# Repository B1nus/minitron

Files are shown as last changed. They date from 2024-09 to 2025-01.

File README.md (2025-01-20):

# Minitron
Turn your Prusa Mini into an upside-down CoreXY 3D Printer. This github repository covers the software side of the project, for build instructions and the bill of materials check out [the printables page](https://www.printables.com/model/1022602-minitron).

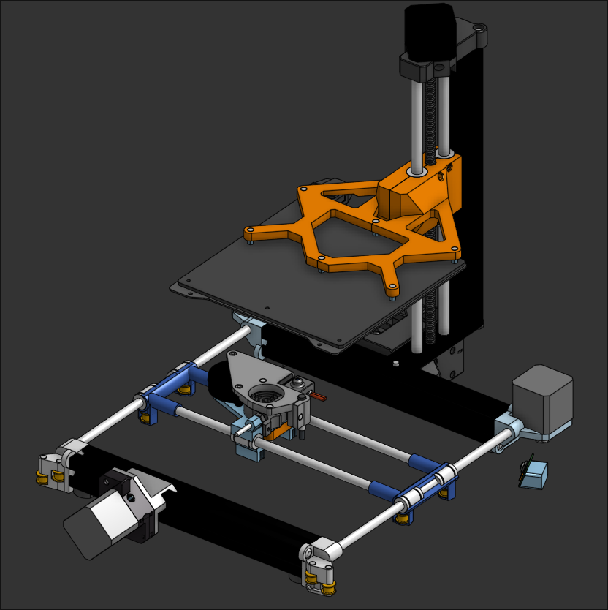
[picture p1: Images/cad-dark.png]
Screenshot of the positron CAD project


# Minitron in action
Gif of the minitron printing

# The first print
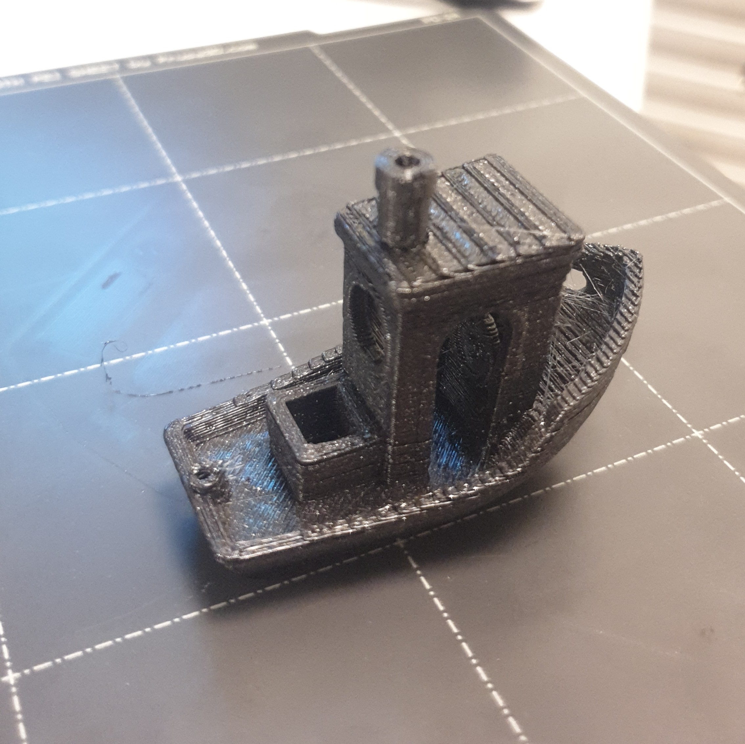
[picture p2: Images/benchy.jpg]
Picture of my first successfull print on the minitron


# WARNING!
The printer does work, but there are problems with this design:
- Loose belts (add an adjustable belt tension on the corner pieces)
- slanted and wobbly bed (add more plastic)
- extruder cable too short (use an extension cable)

# MainsailOS
MainsailOS is the operating system you will run on your control board (the raspberry pi). Mainsail handles the webinterface, scheduling prints, sending gcode and basically anything except communication with hardware which is the Buddy Boards job. [Install Mainsail here](https://docs-os.mainsail.xyz/getting-started/raspberry-pi-os-based). If you don't fell comfortable with Klipper and Mainsail you can try [this modified buddy board firmware](https://github.com/Snake-Edition/P32-FW/releases). Please note that you won't have a place to mount the LCD screen, as this printer is designed to use Mainsail's web interface instead of the LCD.

If you're using the rtl8188eu wifi adapter you should follow [these instruction](#rtl8188eu) to get wifi working.

## Installing Klipper
To install third party firmware you need to put your printer into DFU mode. Do this by following [the official instructions](https://help.prusa3d.com/article/flashing-custom-firmware-mini_14). Basically you need to cut the appendix and then short circuit two pins at the same time as switching on the printer. Connect the printer to your Raspberry Pi and proceed with these commands:

First run `$ cd ~/klipper`
Then `$ make menuconfig` and choose:
- Enable extra low-level configuration options
- STMicroelectronics STM32
- STM32F407
- No Bootloader
- Clock Reference 12 Mhz crystal
- Communication interface USB (on PA11/PA12)

Now run `lsusb` and look for a device with "DFU" in the name. If you can't find it, chances are the printer is not in DFU mode or the cable to the printer isn't working. To check if the printer is in DFU mode, turn it off and connect the LCD to the board. After putting it into DFU mode the screen should be blinding white.

When you've found the DFU device run `make flash FLASH_DEVICE=[insert id here]` with the id you found with `lsusb`.

# Configuration
My printer configuration is backed up automatically to this repository in *printer_data/config*. Feel free to use my config files. Don't forget to change the `rotation_distance` to `32` in the *printer.cfg* file if you're using the stock extruder. My prusa slicer profiles are also in this repository in the folder *prusa_profiles*.

Learn more about Klipper from their [documentation](https://www.klipper3d.org/pressure_advance.html).

# Extras
## Custom extruder and lid
I have some more [prusa mini mods on my printables account](https://www.printables.com/@Binus_2239073/models). It's up to you if you want these mods as well. The stock parts work just fine to.
### Camera
Check crowsnests logs to find the search path to your camera. Set *cam > device* in the file *crowsnest.conf* to this path. Sometimes it takes a while for the camera to load, you might need to refresh the page as well.

### Remote Control (Octoeverywhere)
Follow [their official instructions](https://octoeverywhere.com/dashboard?source=mainsail_docs). To learn of other solutions visit [mainsails page](https://docs.mainsail.xyz/overview/quicktips/remote-access).

### Backups
I broke my sd card once. Not fun. Nowdays I always backup my config files to github with [klipper-backup.git](https://github.com/Staubgeborener/klipper-backup?tab=readme-ov-file). Follow the instructions in their [documentation](https://klipperbackup.xyz/).

# Technical detail
### rtl8188eu
This specific driver caused me some trouble. To fix it, install the driver with this [excellent tutorial](https://gist.github.com/MBing/de297a8ae5e8a191c55a67a568d20d31) by [MBing](https://gist.github.com/MBing). If you want to choose a specific ip address change your /etc/interfaces file to something like this:
```
auto wlan0
iface wlan0 inet static
address [insert ip address]
netmask [insert netmask]
gateway [insert gateway]
broadcast [insert broadcast]
wpa-conf /etc/wpa_supplicant/wpa_supplicant.conf
```
Get the values by running ```ifconfig``` on another device connected to the same wifi.

# Credit
Credit to Prusa for the Prusa Mini, Kralyn for the Positron printer and Voxolite for the JourneyMaker. I wouldn't have been able to make this printer without you.

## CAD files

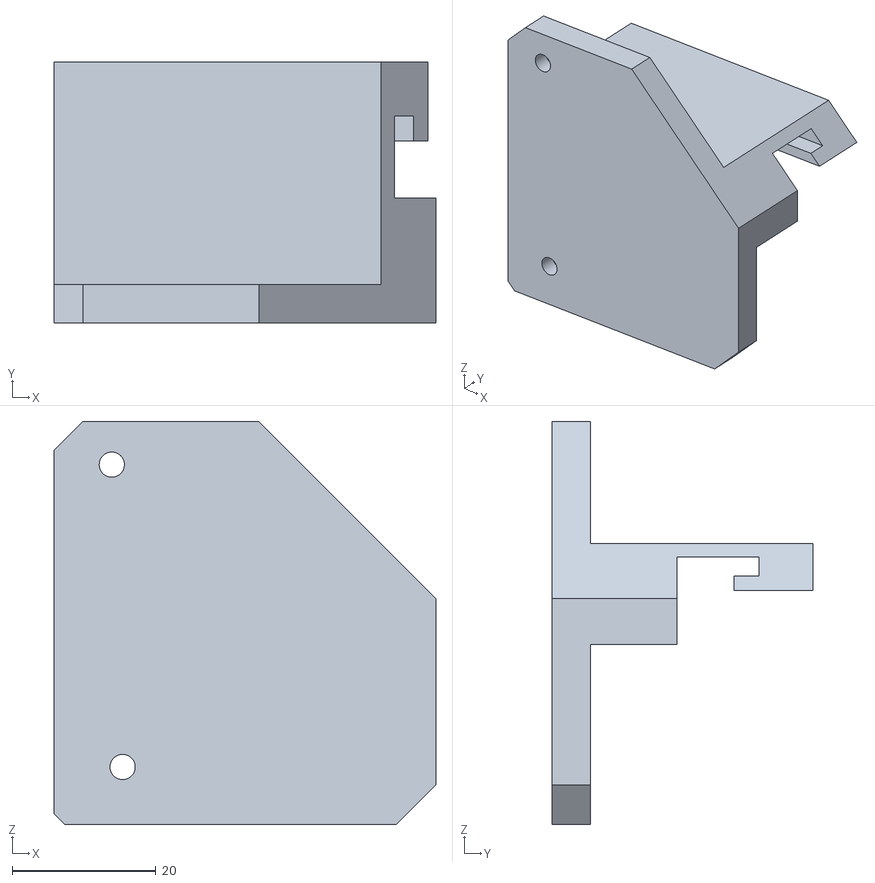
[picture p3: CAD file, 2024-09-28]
CAD/STL/Extruder Mount.stl
53.0 x 36.2 x 56.0

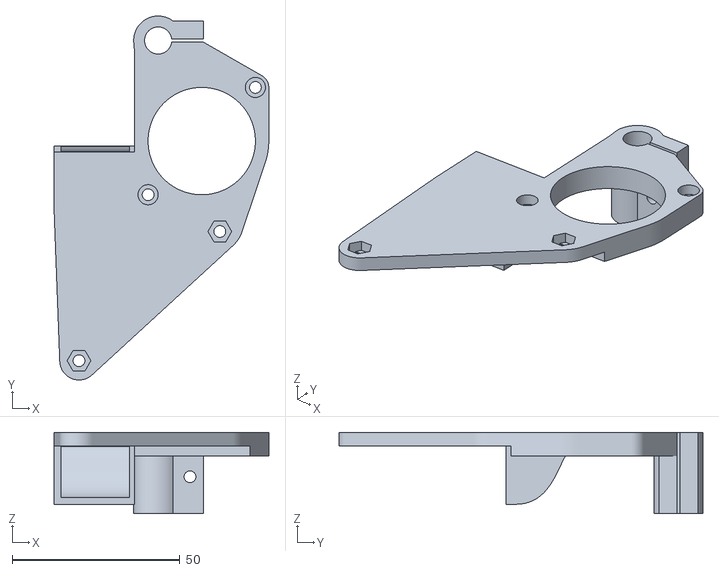
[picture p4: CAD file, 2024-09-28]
CAD/STL/Toolhead Top.stl
64.0 x 108.5 x 24.2

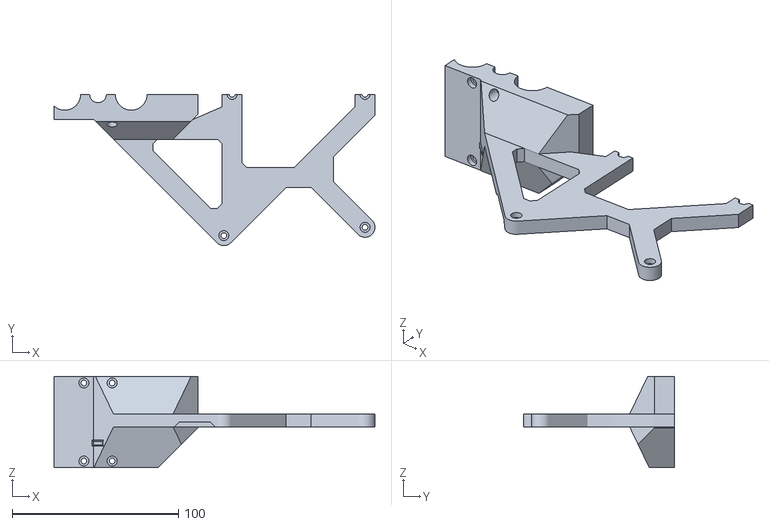
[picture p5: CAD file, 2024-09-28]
CAD/STL/Bed Carriage LEFT.stl
193.2 x 91.0 x 55.0

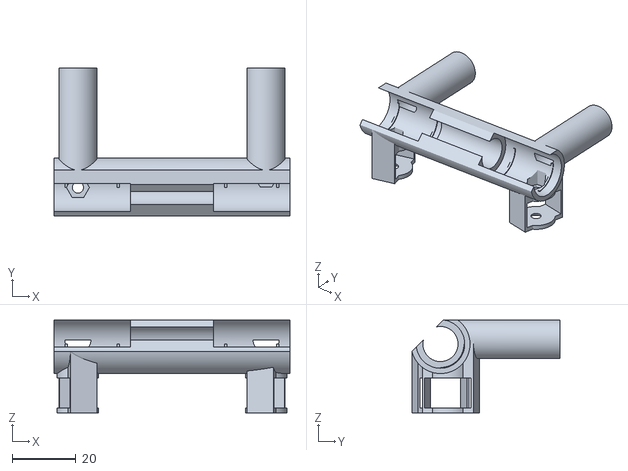
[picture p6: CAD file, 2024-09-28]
CAD/STL/Slider LEFT.stl
74.0 x 46.5 x 29.1

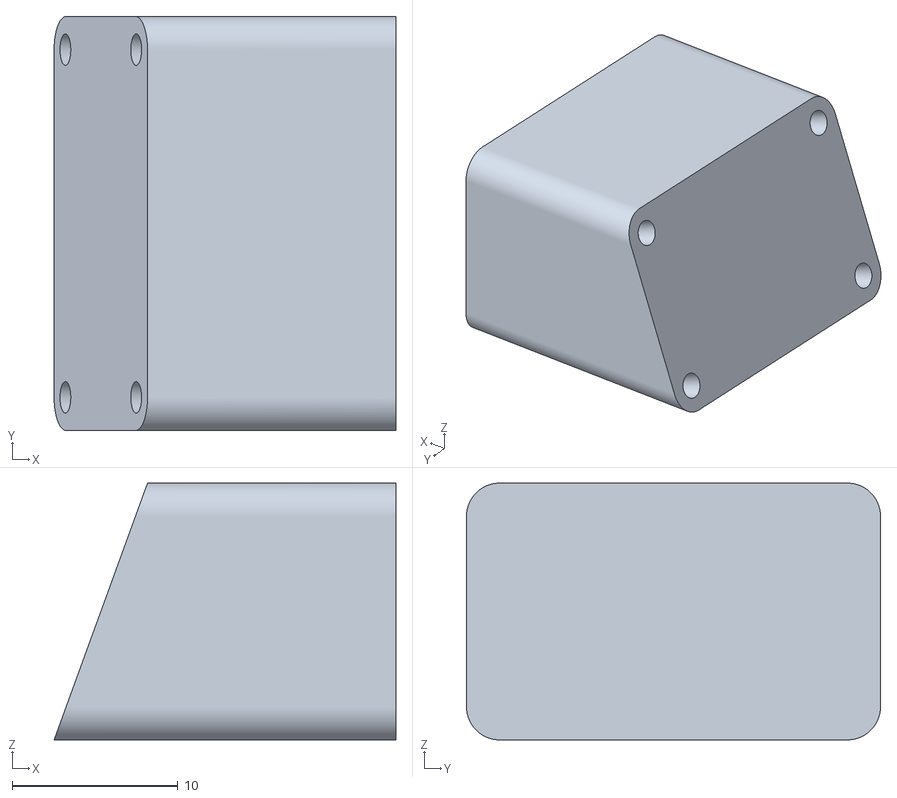
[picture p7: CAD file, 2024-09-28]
CAD/STL/Cam Mount.stl
20.6 x 25.0 x 15.5

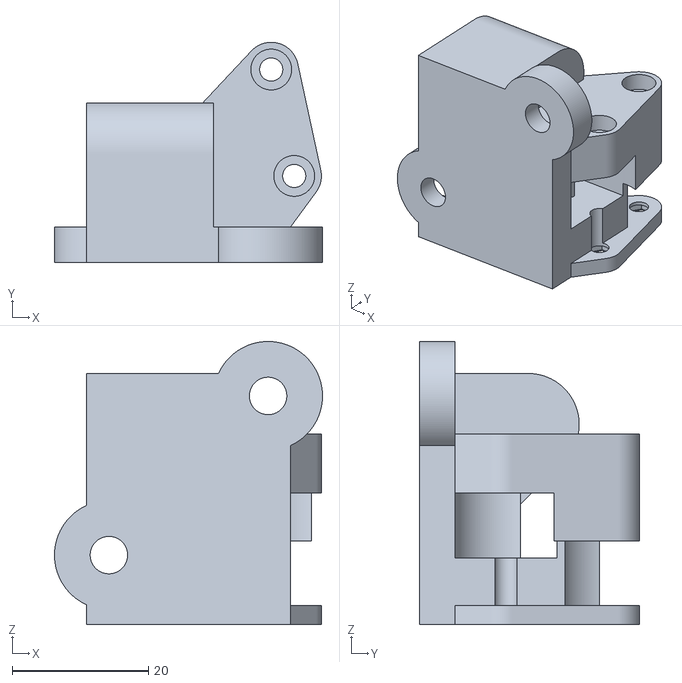
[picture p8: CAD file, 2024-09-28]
CAD/STL/Corner RIGHT.stl
39.4 x 32.4 x 41.6

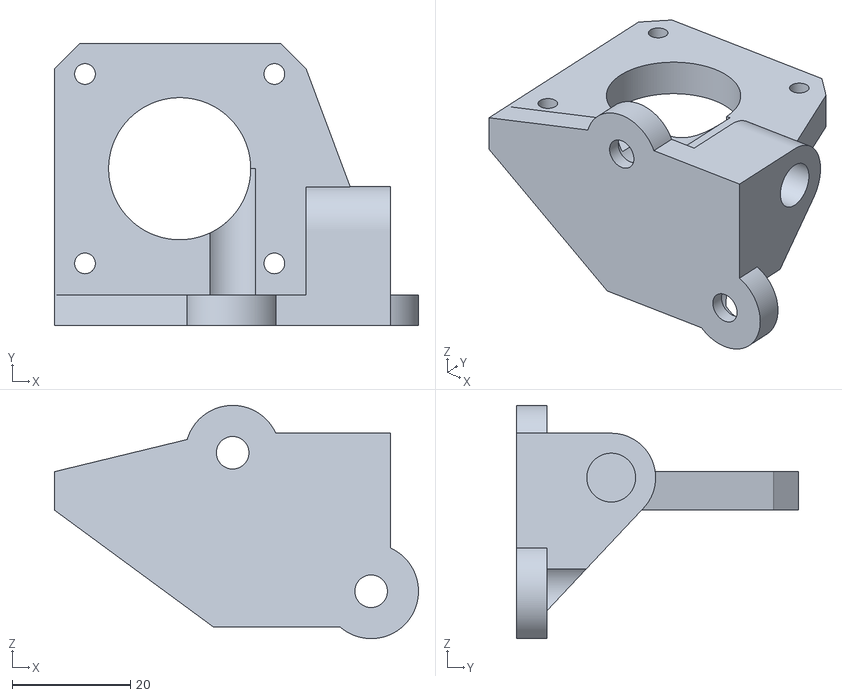
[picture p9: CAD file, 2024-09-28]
CAD/STL/Motor Corner RIGHT.stl
61.5 x 47.6 x 39.4

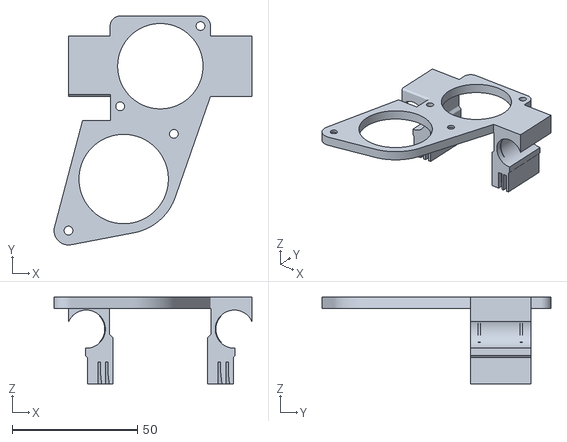
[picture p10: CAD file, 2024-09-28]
CAD/STL/Toolhead Bottom.stl
78.8 x 91.2 x 34.7

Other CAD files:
CAD/STL/Bed Carriage RIGHT.stl
CAD/STL/Slider RIGHT.stl
CAD/STL/Corner LEFT.stl
CAD/STL/Motor Corner LEFT.stl

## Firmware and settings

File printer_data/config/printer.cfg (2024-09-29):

#Exclude object support, needs [file_manager] > enable_object_processing to be enabled in moonraker.cfg
[exclude_object]
[include mainsail.cfg]
[include shell_command.cfg]
[include macros.cfg]

[stepper_x]
step_pin: PD1
dir_pin: PD0
enable_pin: !PD3
microsteps: 16
rotation_distance: 32  # 200 * 16 / 100
endstop_pin: tmc2209_stepper_x:virtual_endstop
position_endstop: 180.4
position_min: -2
position_max: 180.4
homing_speed: 50
homing_retract_dist: 0

[stepper_y]
step_pin: PD13
dir_pin: PD12
enable_pin: !PD14
microsteps: 16
rotation_distance: 32  # 200 * 16 / 100
endstop_pin: tmc2209_stepper_y:virtual_endstop
position_endstop: -3
position_min: -3
position_max: 180
homing_speed: 50
homing_retract_dist: 0

[stepper_z]
step_pin: PD4
dir_pin: !PD15
enable_pin: !PD2
microsteps: 16
rotation_distance: 4
endstop_pin: probe:z_virtual_endstop
position_min: -2.5
position_max: 185

[extruder]
step_pin: PD9
dir_pin: !PD8
enable_pin: !PD10
microsteps: 16
rotation_distance: 23.1221 # Use the value 32 if you're using the stock extruder
nozzle_diameter: 0.400
filament_diameter: 1.750
heater_pin: PB1
sensor_type: ATC Semitec 104GT-2
sensor_pin: PC0
#control: pid
#pid_kp: 18.634
#pid_ki: 0.941
#pid_kd: 92.238

# TEMPORARY
min_temp: -100
# TEMPORARY

max_temp: 270
max_extrude_only_distance: 500

[tmc2209 stepper_x]
uart_pin: PD5
uart_address: 1
diag_pin: ^PE2
driver_SGTHRS: 130
run_current: 0.35
sense_resistor: 0.22
stealthchop_threshold: 999999

[tmc2209 stepper_y]
uart_pin: PD5
uart_address: 3
diag_pin: ^PE1
driver_SGTHRS: 130
run_current: 0.4
sense_resistor: 0.22
stealthchop_threshold: 999999

[tmc2209 stepper_z]
uart_pin: PD5
uart_address: 0
diag_pin: ^PE3
driver_SGTHRS: 100
run_current: 0.35
sense_resistor: 0.22
stealthchop_threshold: 999999

[tmc2209 extruder]
uart_pin: PD5
uart_address: 2
diag_pin: ^PA15
driver_SGTHRS: 100
run_current: 0.375
sense_resistor: 0.22

[heater_bed]
heater_pin: PB0
sensor_type: EPCOS 100K B57560G104F
sensor_pin: PA4
control: pid
# Prusa's firmware defaults.
pid_Kp: 120
pid_Ki: 1.5
pid_Kd: 600

# TEMPORARY
min_temp: -100
# TEMPORARY

max_temp: 110

# Hotend fan.
# The stock firmware uses control ranges of PWM 0-50%, RPM 1000-8000.
# Change fan_speed below to match your preference. Measured speeds:
#   fan_speed 0.5:  50% PWM = 4000RPM (Prusa stock default speed)
#   fan_speed 1.0: 100% PWM = 8000RPM (safe but loud)
[heater_fan hotend_fan]
pin: PE9
tachometer_pin: PE14
fan_speed: 0.55

# Part cooling fan.
# The stock firmware uses control ranges of PWM 10-50%, RPM 500-5000.
# To match stock firmware, set the Klipper fan speed to 50%. This speed
# can be safely increased to 100% for better part cooling. Measured speeds:
#    50% PWM = 2500RPM (Prusa stock default speed)
#   100% PWM = 5000RPM (better cooling, still quiet)
[fan]
pin: PE11
tachometer_pin: PE10

# The SuperPINDA has built-in temperature compensation and no thermistor output,
# so no compensation table is needed here.
[probe]
pin: PA8
# TO BE DETERMINED
# x_offset: 21
# y_offset: -21.3
# z_offset: 0  # set this to your Live Z Offset, but negated (invert the sign)
speed: 6.0

[safe_z_home]
home_xy_position: 147.4, 21.1
z_hop: 4

[bed_mesh]
speed: 100
horizontal_move_z: 5
mesh_min: 10, 10
mesh_max: 141, 167
probe_count: 4, 4
#adaptive_margin: 5 # Not needed

[filament_switch_sensor filament_sensor]
switch_pin: ^PB4
pause_on_runout: True

[mcu]
serial: /dev/serial/by-id/usb-Klipper_stm32f407xx_440048001050315239353820-if00
restart_method: command

[printer]
kinematics: corexy
max_velocity: 120
max_accel: 1250
max_z_velocity: 14
max_z_accel: 440

[input_shaper]
shaper_type_x: zv
shaper_type_y: 2hump_ei
# Prusa firmqare defualts.
shaper_freq_x: 118.0
shaper_freq_y: 32.0

# G2 and G3 gcode support
[gcode_arcs]
resolution: 0.25 #mm

#*# <---------------------- SAVE_CONFIG ---------------------->
#*# DO NOT EDIT THIS BLOCK OR BELOW. The contents are auto-generated.
#*#
#*# [probe]
#*# z_offset = 1.350
#*#
#*# [extruder]
#*# control = pid
#*# pid_kp = 17.853
#*# pid_ki = 0.763
#*# pid_kd = 104.438
#*#
#*# [bed_mesh default]
#*# version = 1
#*# points =
#*# 	0.397500, 0.116250, 0.110000, 0.061250
#*# 	0.230000, 0.132500, 0.035000, 0.133750
#*# 	0.091250, 0.037500, 0.023750, 0.178750
#*# 	-0.057500, -0.106250, -0.022500, 0.077500
#*# x_count = 4
#*# y_count = 4
#*# mesh_x_pps = 2
#*# mesh_y_pps = 2
#*# algo = lagrange
#*# tension = 0.2
#*# min_x = 10.0
#*# max_x = 140.98
#*# min_y = 10.0
#*# max_y = 166.99

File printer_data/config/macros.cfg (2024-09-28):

######################################################################
# Start Print and End Print
######################################################################

# Replace the slicer's custom start and end g-code scripts with
# START_PRINT and END_PRINT. See docs/Slicers.md for more information on using these macros.

[gcode_macro START_PRINT]
gcode:
    {% set BED_TEMP = params.BED_TEMP|default(60)|float %}
    {% set EXTRUDER_TEMP = params.EXTRUDER_TEMP|default(190)|float %}
    # Wait for bed to reach temperature
    M190 S{BED_TEMP}
    # Use absolute coordinates
    G90
    # Reset the G-Code Z offset (adjust Z offset if needed)
    SET_GCODE_OFFSET Z=0.0
    # Home the printer
    G28
    # Bed Mesh Calibration
    BED_MESH_CALIBRATE ADAPTIVE=1
    # Move the nozzle very close to the bed
    G1 Z0.15 F300
    # Set and wait for nozzle to reach temperature
    M109 S{EXTRUDER_TEMP}

[gcode_macro END_PRINT]
gcode:
    # Turn off bed, extruder, and fan
    M140 S0
    M104 S0
    M106 S0
    # Move nozzle away from print while retracting
    G91
    G1 X-2 Y-2 E-3 F300
    # Raise nozzle by 10mm
    G1 Z10 F3000
    G90
    # Disable steppers
    M84

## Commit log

2024-08-15 Firmware instructions and Resources
    [printer.cfg]
2024-08-15 G2 and G3 support
    [printer.cfg]
2024-08-17 Update printer.cfg gear ratio
    [printer.cfg]
2024-08-17 Update printer.cfg rotation distance for dual gear drive
    [printer.cfg]
2024-09-28 CAD files
    [Bed Carriage LEFT.stl, Bed Carriage RIGHT.stl, Cam Mount.stl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]
2024-09-29 New Backup on boot - 29/09/24 - 00:33:43
    [printer.cfg]
2024-09-29 printer.cfg modified - 29/09/24 - 01:16:19
    [printer.cfg]
2024-09-29 printer.cfg modified - 29/09/24 - 12:48:54
    [printer.cfg]
2024-09-29 printer.cfg modified - 29/09/24 - 13:39:08
    [printer.cfg]
2024-09-29 printer.cfg modified - 29/09/24 - 13:42:03
    [printer.cfg]
2024-09-29 New backup from 29/09/24 - 13:52:00
    [Bed Carriage LEFT.stl, Bed Carriage RIGHT.stl, Cam Mount.stl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]
2024-09-29 printer.cfg modified - 29/09/24 - 15:21:43
    [Bed Carriage LEFT.stl, Bed Carriage RIGHT.stl, Cam Mount.stl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]
2024-09-29 printer.cfg modified - 29/09/24 - 15:21:55 - No new changes pushed
2024-09-29 Move back files
    [Bed Carriage LEFT.stl, Bed Carriage RIGHT.stl, Cam Mount.stl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]
2024-09-29 printer.cfg modified - 29/09/24 - 15:34:54
    [printer.cfg]
2024-09-29 printer.cfg modified - 29/09/24 - 15:35:12 - No new changes pushed
2025-01-20 Update README.md problem after first prototype
2025-01-20 Added gif of the prototype printing
2025-01-20 Update README.md printables link
2025-01-20 image of my first print on the minitron! (:
2025-01-20 Update README.md image of first print! :D
